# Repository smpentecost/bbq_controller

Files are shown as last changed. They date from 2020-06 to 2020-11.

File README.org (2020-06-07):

* Automated BBQ Controller

This project brings my BBQ/smoker into the 21st century, by automating control of its airflow damper based on the smoker's current temperature. My parts list:

1. 1x Raspberry Pi Zero W - $10
2. 1x SD card loaded with Raspbian Lite - $5
3. 2x SainSmart MAX6675 Module + K Type Thermocouple Thermocouple Sensor Temperature 0~1024℃ - $14ea
4. 1x Futaba S3003 Servo - $18
5. 1x 5-in HVAC Damper Duct Manual Volume Damper with Sleeve - $15
6. 1x MCIGICM IC 7805 Voltage Regulator, L7805 Linear Positive Fixed 1 Output 5V 1.5A - $0.50ea
7. 1x Custom adapter board - Free since I had parts laying around
8. 1x 9V 1A Power Supply - $10

Pictures of the adapter board details to come soon.

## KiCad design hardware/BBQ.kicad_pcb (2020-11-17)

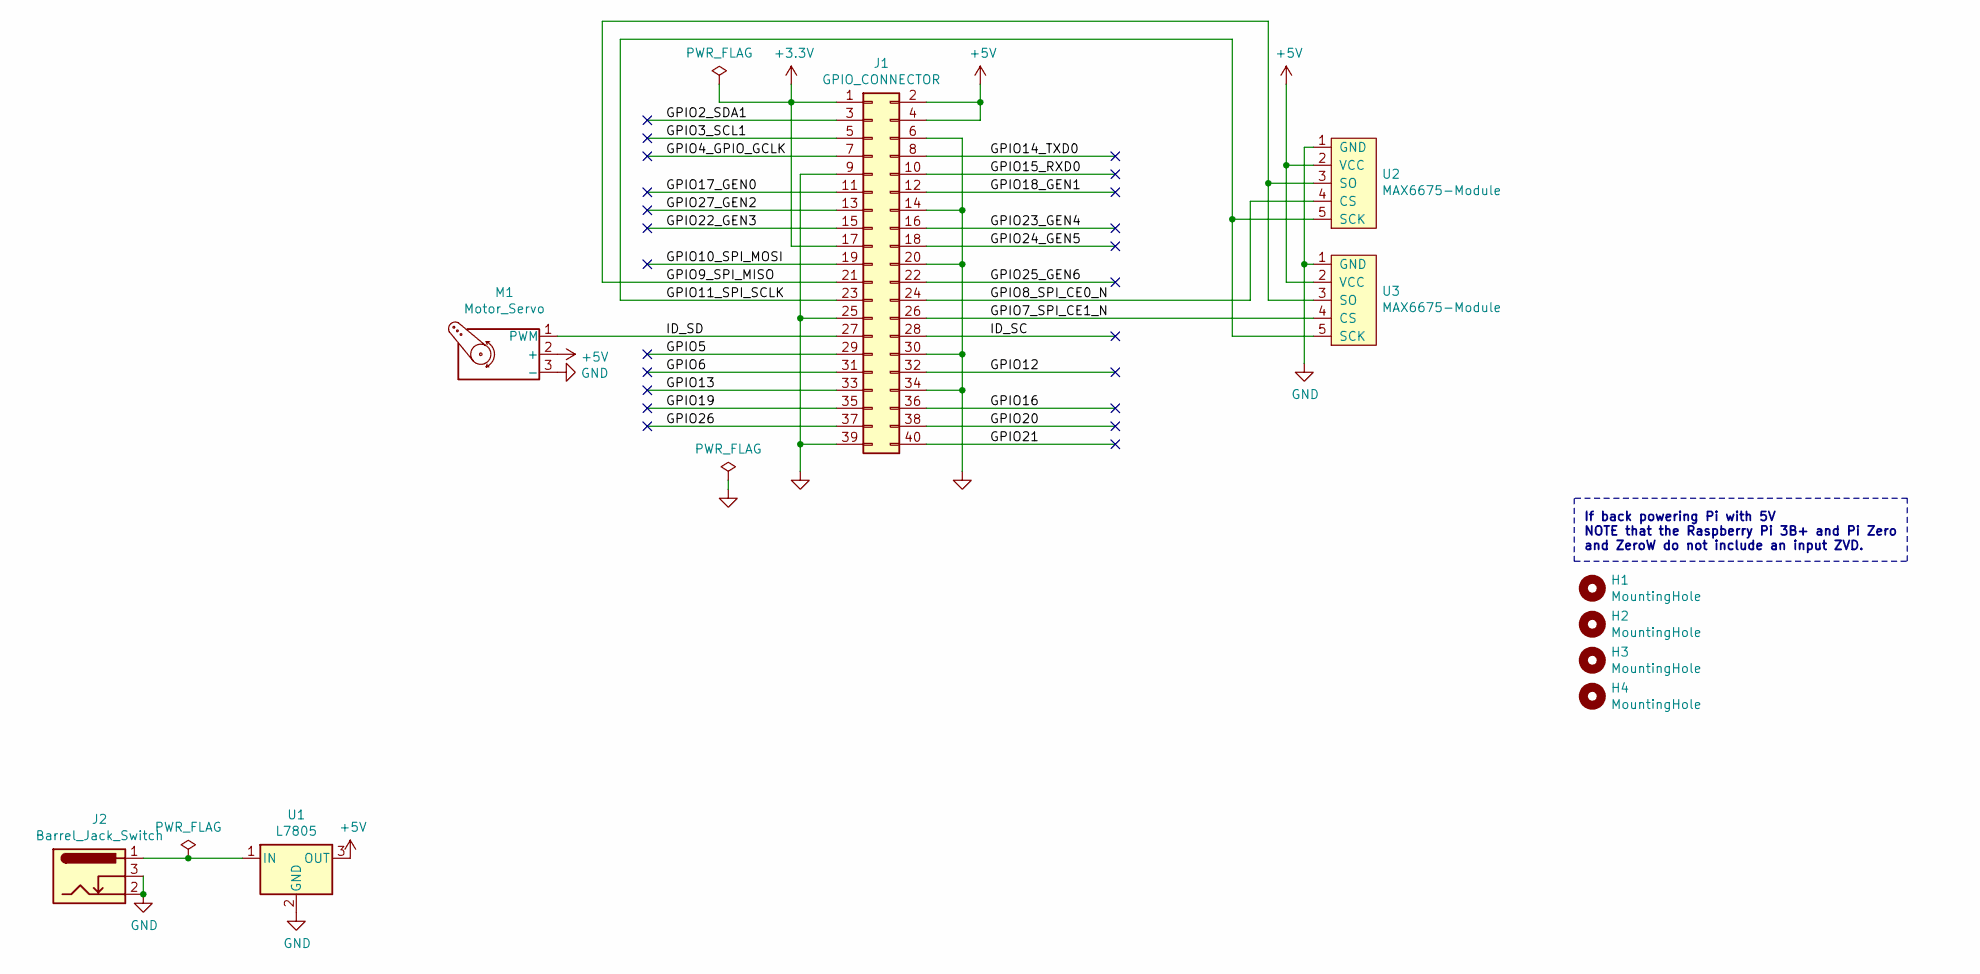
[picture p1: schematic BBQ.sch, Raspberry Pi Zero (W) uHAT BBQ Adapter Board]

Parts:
H1, H2, H3, H4: MountingHole; MountingHole_2.7mm_M2.5_uHAT_RPi
J1: GPIO_CONNECTOR; PinSocket_2x20_P2.54mm_Vertical_Centered_Anchor
J2: Barrel_Jack_Switch; TestPoint_2Pads_Pitch5.08mm_Drill1.3mm
M1: Motor_Servo; PinHeader_1x03_P2.54mm_Vertical
U1: L7805; TO-220-3_Horizontal_TabDown
U2, U3: MAX6675-Module; PinHeader_1x05_P2.54mm_Vertical

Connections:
+3V3: J1.1, J1.17
+5V: J1.2, J1.4, M1.2 (+), U1.3 (OUT), U2.2 (VCC), U3.2 (VCC)
/GPIO2_SDA1: J1.3
/GPIO3_SCL1: J1.5
/GPIO4_GPIO_GCLK: J1.7
/GPIO5: J1.29
/GPIO6: J1.31
/GPIO7_SPI_CE1_N: J1.26, U3.4 (CS)
/GPIO8_SPI_CE0_N: J1.24, U2.4 (CS)
/GPIO9_SPI_MISO: J1.21, U2.3 (SO), U3.3 (SO)
/GPIO10_SPI_MOSI: J1.19
/GPIO11_SPI_SCLK: J1.23, U2.5 (SCK), U3.5 (SCK)
/GPIO12: J1.32
/GPIO13: J1.33
/GPIO14_TXD0: J1.8
/GPIO15_RXD0: J1.10
/GPIO16: J1.36
/GPIO17_GEN0: J1.11
/GPIO18_GEN1: J1.12
/GPIO19: J1.35
/GPIO20: J1.38
/GPIO21: J1.40
/GPIO22_GEN3: J1.15
/GPIO23_GEN4: J1.16
/GPIO24_GEN5: J1.18
/GPIO25_GEN6: J1.22
/GPIO26: J1.37
/GPIO27_GEN2: J1.13
/ID_SC: J1.28
/ID_SD: J1.27, M1.1 (PWM)
GND: J1.6, J1.9, J1.14, J1.20, J1.25, J1.30, J1.34, J1.39, J2.2, J2.3, M1.3 (-), U1.2 (GND), U2.1 (GND), U3.1 (GND)
unnamed: J2.1, U1.1 (IN)

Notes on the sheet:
If back powering Pi with 5V NOTE that the Raspberry Pi 3B+ and Pi Zero and ZeroW do not include an input ZVD.

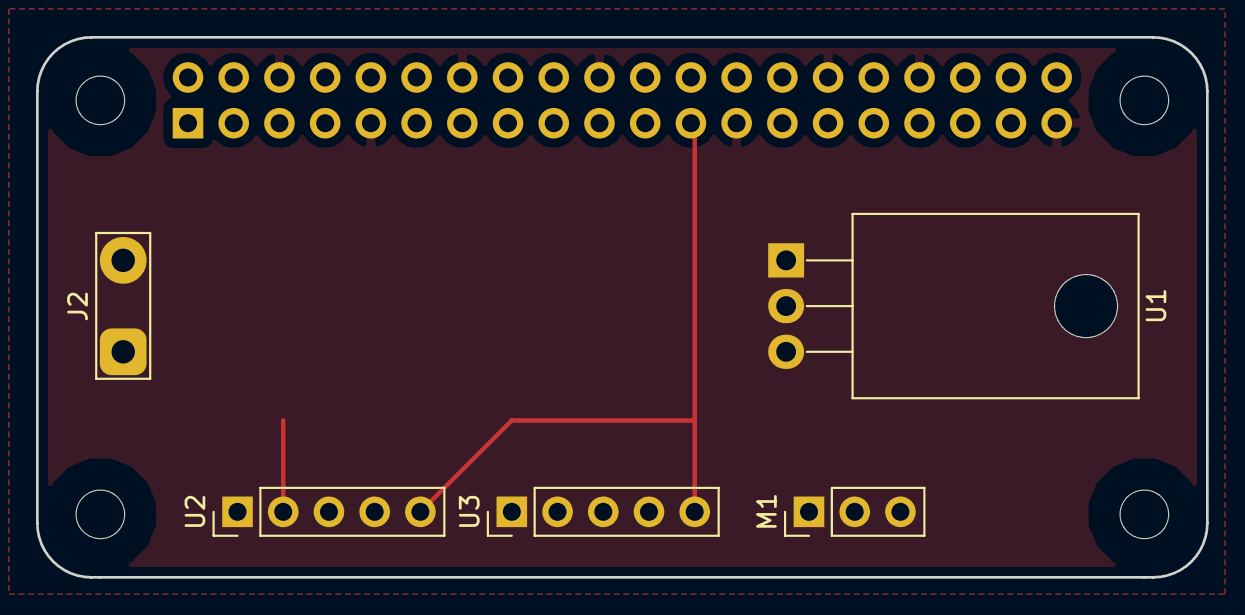
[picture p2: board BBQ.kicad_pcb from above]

Board: 2 copper layers, 65.0 x 30.0 mm, 10 parts (1 on the bottom side), 9 nets.

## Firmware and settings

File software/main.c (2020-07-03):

#include <stdio.h>
#include <stdlib.h>
#include <unistd.h>

#include "controller.h"
#include "psql.h"

int main(int argc, char *argv[]){

  int damper = 0;
  float temp0 = 0.0;
  float temp1 = 0.0;
  float set_temp = 0;
  
  int *spiHandle0 = malloc(4);
  int *spiHandle1 = malloc(4);

  if (argc != 2){
    fprintf(stderr, "Set temperature required.\n");
    return -1;
  } else {
    set_temp = atof(argv[1]);
    fprintf(stdout, "Set temp to %f fahrenheit.\n", set_temp);
  }

  if (initController(spiHandle0, spiHandle1) != 0) exit(-1);

  
  PGconn *conn = initdb();

  sendTemperatures(conn, 150.0, 150.0);

  getTemperatures(conn);
    
  exit_nicely(conn);
  
  
  while (1==1){
    temp0 = getTemp(spiHandle0);
    temp1 = getTemp(spiHandle1);
    fprintf(stdout, "temp0 = %f\n", temp0);
    fprintf(stdout, "temp1 = %f\n", temp1);
    if (temp0 < set_temp){
      if (damper < 100){
  	damper++;
      }
    } else if (temp0 > set_temp){
      if (damper > 0){
  	damper--;
      }
    }
    setDamperOpen(damper);
    sleep(DAMPERPERIOD);
  }
    
  closeHandles(spiHandle0, spiHandle1);
  free(spiHandle0);
  free(spiHandle1);

  return 0;
}

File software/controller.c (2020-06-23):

/*
   gcc -pthread -o spi-pigpio-speed spi-pigpio-speed.c -lpigpio

   sudo ./spi-pigpio-speed [bytes [bps [loops] ] ]
*/

#include <stdio.h>
#include <stdlib.h>
#include <pigpio.h>

#include "controller.h"

int initController(int *handle0, int *handle1)
{
  if (gpioInitialise() < 0){
    fprintf(stderr, "Failed to initialize GPIOs.\n");
    return -1;
  } else {
    fprintf(stdout, "Initialized GPIOs.\n");
  }

  if (gpioGetMode(SERVOPIN) != PI_OUTPUT){
    gpioSetMode(SERVOPIN, PI_OUTPUT);
  }

  *handle0 = spiOpen(THERMOCHAN0,
		     THERMOBAUD,
		     THERMOFLAGS);

  *handle1 = spiOpen(THERMOCHAN1,
		     THERMOBAUD,
		     THERMOFLAGS);

  return 0;
}

void closeHandles(int *handle0, int *handle1)
{
  spiClose(*handle0);
  spiClose(*handle1);
}

/*
 * Sets the open percentage of the damper. 
 * percent - should be between 0 and 100
 * return - 0 (success) or -1 (failure)
 */
int setDamperOpen(int percent)
{
  int servo_pos;
  
  if (percent<0 || percent>100){
    fprintf(stderr, "WARNING: Damper percent should be between 0 and 100.\n");
    return -1;
  } else {
    servo_pos = 2300 - (percent * 9);
  }

  fprintf(stdout, "Setting damper to %d%%.\n", percent);
  if (gpioServo(SERVOPIN, servo_pos) < 0){
    fprintf(stderr, "Issue setting PWM.");
    return -1;
  }
  return 0;
}

/*
 * Get the temp given an spi_handle
 * handle - spi_handle value
 */
float getTemp(int *spiHandle)
{
  char buf[THERMOWORDS];
  float temp = 0.0;   /* temperature in degrees fahrenheit */

  spiRead(*spiHandle, buf, THERMOWORDS);
  temp = (((buf[0] << 8) | buf[1]) >> 3) * 0.25 * (9.0/5.0) + 32.0;
  return temp;
}

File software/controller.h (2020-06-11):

#define SERVOPIN 0 //BCM - PWM0
#define SERVOFREQ 50 //Hz

#define THERMOCHAN0 0 //Channel for THERMO0
#define THERMOCHAN1 1 //Channel for THERMO1
#define THERMOWORDS 2 //Words to read
#define THERMOBAUD 50000 //THERMO SPI BAUD
#define THERMOFLAGS 0 //Set all flags to 0 for default

#define DAMPERPERIOD 1 //Damper period in seconds

int initController(int *handle0, int *handle1);

int setDamperOpen(int percent);

float getTemp(int *spiHandle);

void closeHandles(int *handle0, int *handle1);

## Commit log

2020-02-29 controller working with spi and servo
2020-11-17 added hardware
    [BBQ.kicad_pcb, BBQ.sch]

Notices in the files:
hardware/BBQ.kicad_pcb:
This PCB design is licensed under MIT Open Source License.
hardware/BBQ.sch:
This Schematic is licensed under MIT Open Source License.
